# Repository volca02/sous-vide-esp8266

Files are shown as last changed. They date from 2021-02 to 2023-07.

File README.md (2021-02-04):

# sous-vide-esp8266

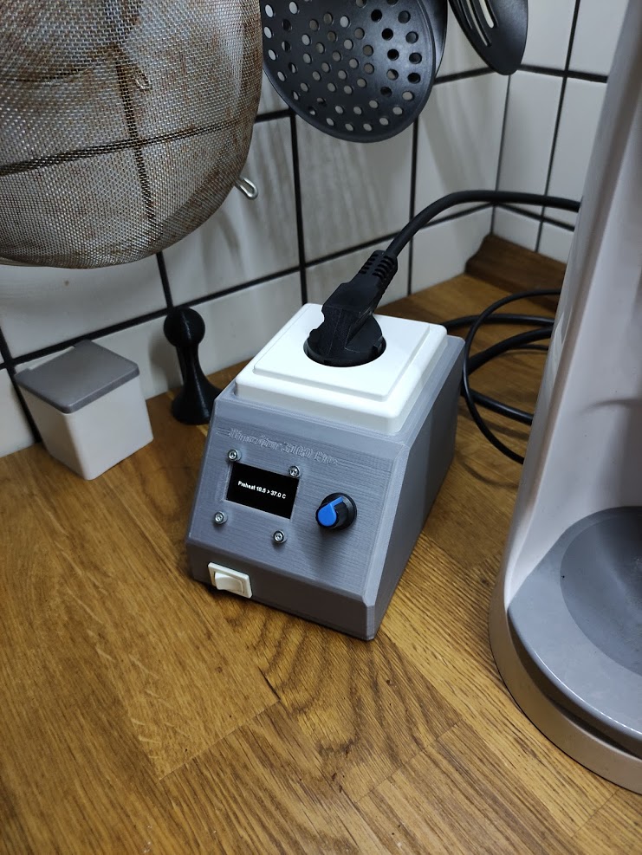
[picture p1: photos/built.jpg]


This project implements a simple timer and PID controller for a dumb slow cooker to become both a timer enabled slow cooker and a simple sous-vide cooker.

## About

The goal is to have a solid state relay control a simple crock-pot (or other compatible simple slow cooker that comes without any electronics). The usage of such contraption is both to add a timer to that slow cooker, and optionally hold a set temperature (when PID control is enabled in setup screen).

## Materials

You will need a couple of components:
 * [Wemos D1 Mini - or a clone](https://www.aliexpress.com/item/32681374223.html?spm=a2g0s.9042311.0.0.36504c4dLBnw4e)
 * [DS18B20 Waterproof Temp sensor](https://www.aliexpress.com/item/32305869288.html?spm=a2g0s.9042311.0.0.36504c4dLBnw4e)
 * [Solid state relay (DC control, AC output)](https://www.aliexpress.com/item/4000045425145.html?spm=a2g0s.9042311.0.0.36504c4dLBnw4e)
 * [SH1106Spi display](https://www.aliexpress.com/item/32844104782.html?spm=a2g0s.9042311.0.0.27424c4d58Iwcy)
 * [Rotary encoder](https://www.aliexpress.com/item/32915420023.html?spm=a2g0s.9042311.0.0.27424c4d58Iwcy)
 * Power cable
 * 5V power adaptor circuit (i.e. something that converts wall socket power to 5V for the Wemos D1)
 * Your local wall mounted power socket (or a cable power socket)
 * An enclosure - a 3d printable model is in [model/](model/) directory (written in openSCAD) - I used universal pcb mounted into the frame, and an a gutted old phone charger for the power supply (so the power supply mount will have to be modified for your situation). Lacking any other, I used M3/16 screws everywhere but the display, which uses 4x M3/10 screws (16 were too long). Sorry the code is a bit messy.

## Wiring

- `GND` is the D1's ground pin
- `3.3V` is the D1's 3V pin

### Temperature sensor

The Black wire connects to `GND`, Red wire to `3.3V`, Yellow wire to `D4`

### Solid state relay

The DC part connects `-` to `GND`,  `+` to `D8`
The AC part connects one power wire through the relay (as appropriate to your country). Ground wire connects directly through to the output socket.

### Display

These are the display's connections:

 * `D7` - `SDA`
 * `D5` - `SCK`
 * `D3` - `RST`
 * `D1` - `DC`
 * `GND` - `CS`
 * `3.3V` - `VDD`

### Rotary encoder

Due to the limited number of pins, A0 is used as a button detection pin.

 * `3.3V` - pin marked `5V`
 * `GND` - `GND`
 * `A0` - `KEY`
 * `D2` - `S1`
 * `D0` - `S2`

 ### Power adaptor

 The input power gets connected to the power adaptor.
 Power adaptor output connects to `5V` and `GND` leads of the Wemos D1.

### Assembly photos

 Here are some assembly photos for easier orientation:
 
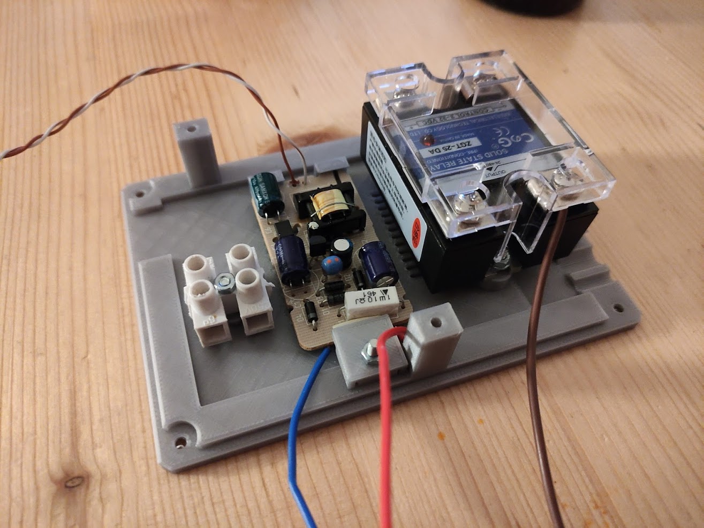
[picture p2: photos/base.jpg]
 
 
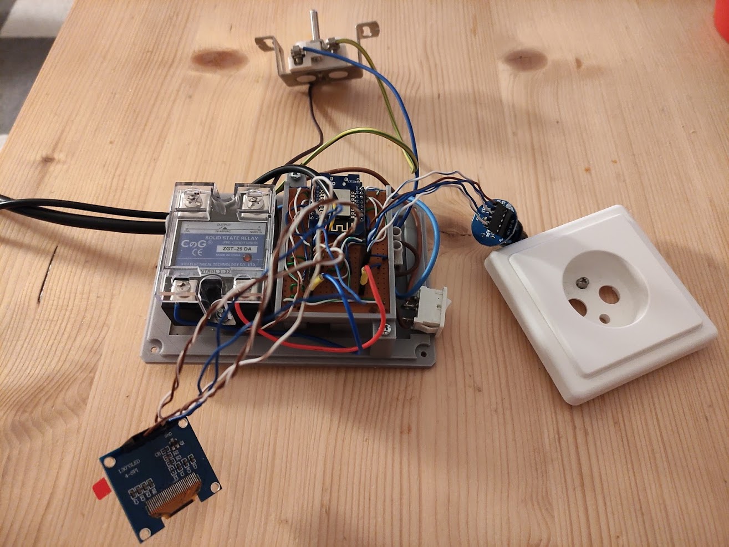
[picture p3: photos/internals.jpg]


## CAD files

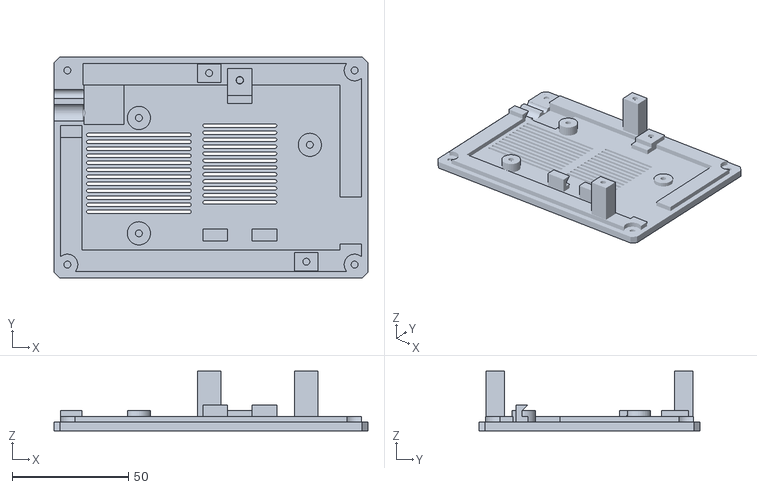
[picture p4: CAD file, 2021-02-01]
model/bottom.stl
135.0 x 95.0 x 25.8

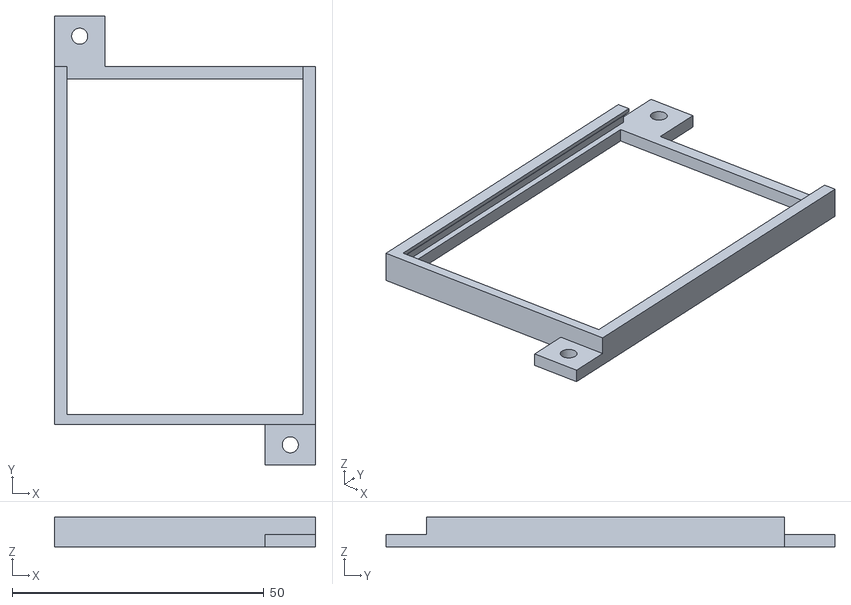
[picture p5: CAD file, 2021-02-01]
model/frame.stl
51.8 x 89.1 x 5.90

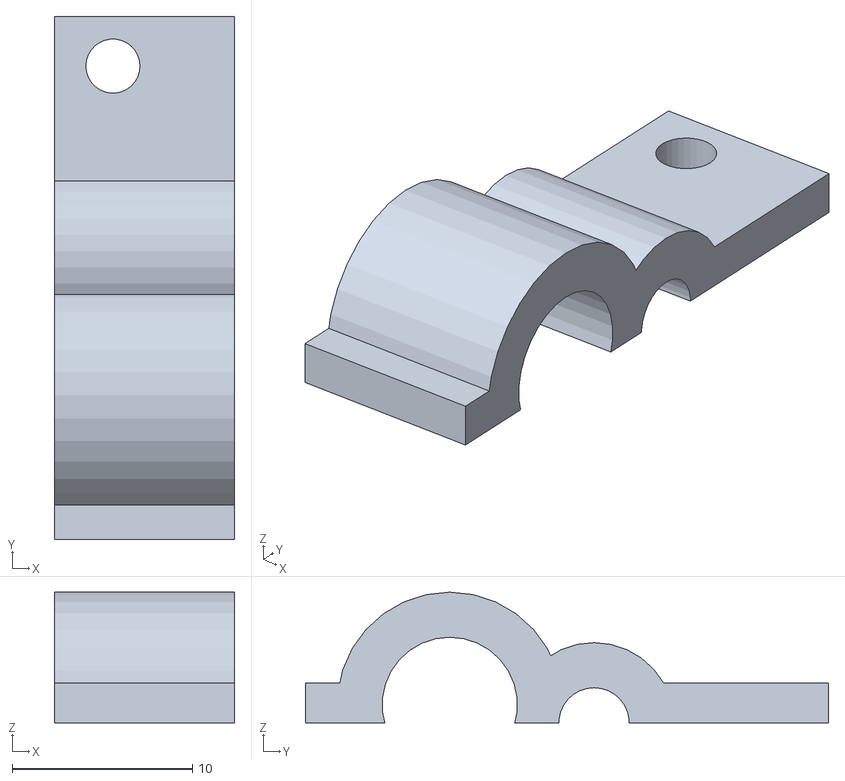
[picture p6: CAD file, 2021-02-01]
model/power_clamp.stl
10.0 x 29.0 x 7.25

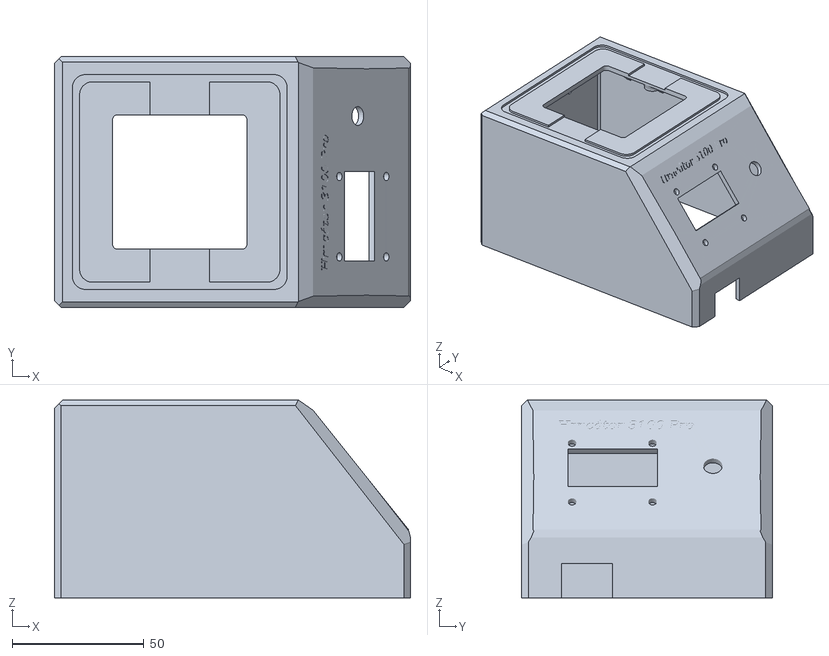
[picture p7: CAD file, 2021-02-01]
model/top.stl
135.0 x 95.0 x 75.0

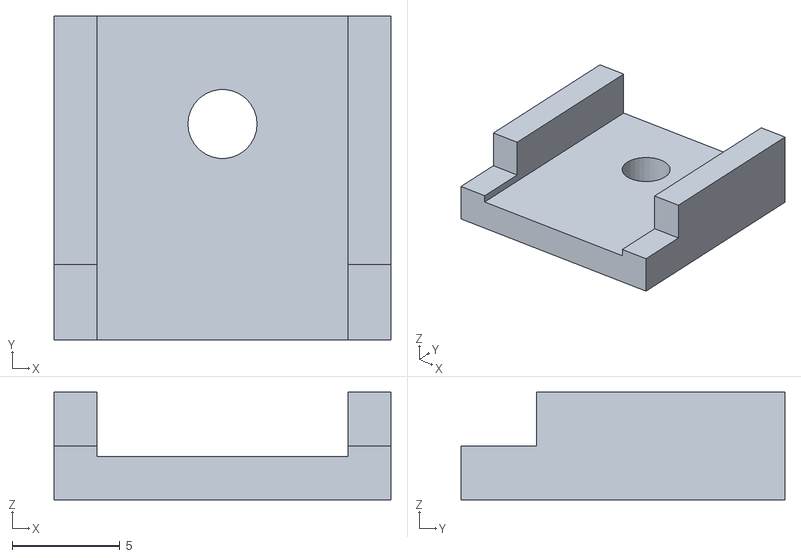
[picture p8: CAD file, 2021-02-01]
model/ps_clamp.stl
15.6 x 15.0 x 5.00

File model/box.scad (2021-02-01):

$fn = 30;

// Dimensions of the base box shape
width = 95;
top_depth = 95;
depth = top_depth + 40;
height = 75;
front_height = height - 50;

fp_angle = 51.3; // todo: use atan or trigonometry to make this in sync

wall = 2.5;
delta = 0.01;

psocket_hole_span = 60;
psocket_hole_d    = 3;
psocket_key_w     = 2.3;
psocket_key_span  = 70;
psocket_hole_h    = 3;

// front panel
encoder_d = 7.2;

// display part dimensions
display_w = 34.0;
display_h = 18.2;

screw_hole_d = 3.2;

// display holes
disp_hole_d = screw_hole_d;

disp_hole_top = 3.0; // above display edge
disp_hole_bottom = 28.5; // relative to the top hole
disp_hole_span   = 30.5; // left to right, centered with display

// switch dimensions
switch_w = 19.5;
switch_ww = 20.1;
switch_h = 13;
switch_lip = 1.2;
switch_x = 15;
switch_depth = 22;

// power supply
ps_w = 31.8;
ps_d = 59;
ps_x = 64;
ps_y = 30;
ps_h = 2.5; // we have to rise the pcb of the ps this much in order to fit the bottom mounted parts

// solid state relay
ssr_w = 45;
ssr_d = 58;
ssr_h = 33;
ssr_x = 14;
ssr_y = 26;

// screw-in mounts
choc_w = 22;
choc_d = 20.5;
choc_h = 18;
choc_x = 99;
choc_y = 20;

// power in lead-in
powin_off = 15.5;
powin_w = 10;
powin_d = 29.5;
powin_cable_d = 7.5;
temp_cable_d = 3.9;
powin_c1_y = 8;
powin_c2_y = 16;
powin_c1_z = 1;
powin_c2_z = 0;

// pcb mount pillars
pcb_x = 101;
pcb_y = -44.5;
pcb_d = 8;
pcb_w = 10;
pcb_h = 22;

// real pcb dimensions
pcb_r_w = 49.3; // slightly more than pcb (48.8) so we can slide it in
pcb_r_l = 66.6;
pcb_r_h = 1.4;

/*

  TODO:
  * test fit:
    X display
    X encoder
    - cable leadin
    - probe leadout
    X switch cutout
    X screw fit

  * mount points
    X ssr
    - power supply
    X main board
    X chocolate

  * models
    - Beautiful knob
  */

module rounded_cube(dim = [], d = 4) {
    // TODO: Use union (4 cylinders, 2 cubes) instead. this is expensive without a good reason
    hull() {
        translate([d/2,d/2,0]) cylinder(d=d, h=dim[2]);
        translate([dim[0]-d/2,d/2,0]) cylinder(d=d, h=dim[2]);
        translate([d/2,dim[1]-d/2,0]) cylinder(d=d, h=dim[2]);
        translate([dim[0]-d/2,dim[1]-d/2,0]) cylinder(d=d, h=dim[2]);
    }
}

module power_socket() {
    translate([-40,-40,0]) difference() {
        union() {
            difference() {
                rounded_cube([80,80,9.8],d=10);
                translate([1.5,1.5,-1.5]) rounded_cube([77,77,9.8]);
            }
            translate([15/2,15/2,9.8]) rounded_cube([65,65,3.5]);
            translate([40,40,-3]) cylinder(d=42.3,h=16);
            translate([20,15,-25]) rounded_cube([40,50,25]);
        }

        translate([40,40,9.8+3.5-16+delta]) cylinder(d=38.5,h=16);
    }
}

// power socket frame - subtracted from the top panel to allow the socket
// to be slightly (1mm) inserted into the panel
module socket_frame(h=2) {
    wid = 81.5;
    iwid = 76;
    dif = wid-iwid;
    translate([-wid/2,-wid/2,0]) difference() {
        rounded_cube([wid,wid,h],d=10);
        translate([dif/2,dif/2,-0.1]) rounded_cube([iwid,iwid,h+0.2],d=9.8);
    }
}

module bracket(h=0.5) {
    br_w = 14.1;
    br_h = 22.5;

    difference() {
        union() {
            translate([br_w/2,0,h/2]) cube([br_w,br_h,h],center=true);
            translate([6.05,0,-wall-0.2]) cylinder(d=psocket_hole_d,h=wall,$fn=30);
        }
      //  translate([11.0+3.3/2,0,-delta+h/2]) cube([3.3,psocket_key_w,h+0.2],center=true);
    }
}

module mounting_brackets(h=0.5) {
    sp   = 47.9;

    // spaced
    for (a=[0,180]) rotate([0,0,a]) translate([sp/2,0,0]) bracket(h);
}

module socket_pillar() {
    extd = psocket_hole_d+2*wall;
    difference() {
        union() {
            cylinder(d=extd,h=psocket_hole_h);
            translate([0,0,psocket_hole_h-2]) cylinder(d2=extd+1,d1=extd,h=2);
        }
        translate([0,0,-0.1]) cylinder(d=psocket_hole_d,h=psocket_hole_h+0.2);
    }
}

module mounting_pillars(h=0.5) {
    sp   = psocket_hole_span;

    // spaced
    for (a=[0,180]) rotate([0,0,a]) translate([sp/2,0,0]) socket_pillar();
}

// positive geometry wall power socket mount, placed directly on the top surface
module psocket_mount() {
    rotate([0,0,90]) translate([0, -width/2, -wall]) union() {
        difference() {
            union() {
                cube([top_depth, width, wall]);
                // strengthening for the nuts/bolts
                translate([top_depth/2,width/2,-psocket_hole_h]) mounting_pillars();
            }
            translate([top_depth/2,width/2,0]) {
                translate([0,0,wall-1]) socket_frame();
                translate([-51/2,-51/2,-delta]) rounded_cube([51,51,10]);
                translate([0,0,wall-1]) mounting_brackets(h=1+delta);

            }
        }
    }
}

module side_shape() {
    polygon([
                    [0,0],
                    [0,height],
                    [top_depth, height],
                    [depth, front_height],
                    [depth, 0]
            ]);
}

module base_shape() {
    translate([0,width/2,0]) rotate([90,0,0]) linear_extrude(height=width) side_shape();
}


module inner_cavity() {
    translate([0,width/2,0]) difference() {
        w2 = 2*wall;
        union() {
            translate([0,-wall,0]) rotate([90,0,0]) linear_extrude(height=width-w2) offset(r=-wall) side_shape();
            translate([wall,-width+wall,-delta]) cube([depth-w2,width-w2,3*wall]);
        }

        for (x=[20,40,60,80]) {
            translate([x,0,height-20]) rotate([45,0,0]) cube([wall, 40, 40]);
            translate([x,-width-wall,height-20]) rotate([45,0,0]) cube([wall, 40, 40]);
        }
    }
}


//inner_cavity();

//translate([top_depth/2,0,height-1]) power_socket();


module display_cutter() {
    cube([display_w,display_h,2*wall]);
    for(y=[display_h+disp_hole_top,display_h-disp_hole_bottom+disp_hole_top]) {
        for(x=[0,disp_hole_span]) {
            translate([x+disp_hole_d/2,y,0]) cylinder(d=disp_hole_d,h=2*wall);
        }
    }
}


module encoder_cutter() {
    cylinder(d=encoder_d,h=2*wall);
}

module front_panel() {
/*    difference() {*/
//      cube([70,50,wall]);
    union() {
        translate([5,20,-delta]) display_cutter();
        translate([60,30,-delta]) encoder_cutter();
        translate([ 1, 48, wall - 0.15 ]) linear_extrude(height    = 1,
                                                         convexity = 4)
                text("Hrncátor 3100 Pro", font = "DejaVu Serif:style=Italic", size = 4);

        translate([5,17,wall-delta]) cube([display_w,1,1]);
  }
}

module raw_body() {
    align=3.2; // an ugly method for sure, but lets us do the positioning of front panel stuff easier
    union() {
        difference() {
            base_shape();
            inner_cavity();
            translate([0,-width/2,height-wall-delta]) cube([top_depth, width, wall+delta*2]);
//            translate([depth-align,-width/2+25/2,front_height]) rotate([0,0,90]) rotate([fp_angle,0,0]) translate([0,0,-delta]) cube([70,50,2*wall]);
            translate([depth-align,-width/2+25/2,front_height]) rotate([0,0,90]) rotate([fp_angle,0,0]) front_panel();
        }

        translate([top_depth/2,-width/2,height]) psocket_mount();
    }
}

// half of the cutters, mirrored later for accuracy
module cutter_half(offseting=0) {
    off = 5;
    translate([-1+depth/2,width/2+off/2,height + off/2]) rotate([45,0,0]) cube([depth,10-offseting,10-offseting],center=true);
    translate([off/2+top_depth,width/2+off/2,height - off/2]) rotate([0,52,0]) rotate([45,0,0]) cube([depth,10-offseting,10-offseting],center=true);


    translate([top_depth+2,width/2+off/2,height+3]) rotate([0,0,-90]) rotate([55,0,0]) cube([depth,10-offseting,10-offseting],center=true);


    translate([-1,width/2+off/2,height+3]) rotate([0,0,-90]) rotate([45,0,0]) cube([depth,10-offseting,10-offseting],center=true);

    translate([depth+5.3,width/2+off/2,front_height - off/2]) rotate([0,0,-90]) rotate([15,0,0]) cube([depth,10-offseting,10-offseting],center=true);

    // corners
    translate([0,width/2,0]) rotate([0,0,45]) translate([0,0,(height+1)/2]) cube([3.5-offseting,3.5-offseting,height+2],center=true);
    translate([depth,width/2,0]) rotate([0,0,45]) translate([0,0,(height+1)/2]) cube([3.5-offseting,3.5-offseting,height+2],center=true);
}

module cutters(off = 0) {
    cutter_half(off);
    mirror([0,1,0]) cutter_half(off);
}

module pillar(d,w,h,s=-1) {
    dw = d+2*w;
    union() {
        difference() {
            cylinder(d=dw,h=h);
            translate([0,0,-delta]) cylinder(d=d,h=h-dw+2*delta);
            if (s != 0) {
                translate([0,0,h]) rotate([0,-s*45,0]) cube([4*dw,dw,dw], center=true);
            }
        }
    }
}

module pillars(d=3,w=wall,h=22,en=1) {
    // all corners have screw pillars
    pd = 9 + wall;
    for (y = [-width/2+pd/2,width/2-pd/2]) {
        for (x = [pd/2,depth-pd/2]) {
            xs = x - depth/2;
            translate([x,y,0]) pillar(d=d,w=w,h=h,s=en*abs(xs)/xs);
        }
    }
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

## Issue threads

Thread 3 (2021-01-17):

Add temperature history

volca02, 2021-01-17:
Add a simple (1 pt per minute) temperature logger. Memory should be able to hold 1440 float values, if not, convert to fixed point int16_t. Add json url to dump the values for a web based graph or similar.

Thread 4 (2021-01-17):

Add PID tuning code

volca02, 2021-01-17:
A special mode (maybe when encoder is held on bootup) that would do automatic pid tuning and write the result to SPIFFS. Then a code that reads this on bootup and gives these to AutoPID class instance.

This bootup special menu could also be used to set wifi and other things...

volca02, 2021-02-05:
implemented in 4d5d5553b20a85f5fcbc73b2e2dd840e69db3d70, does not work yet. Needs to be fixed

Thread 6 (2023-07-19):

Dependency and build errors

biuklija, 2023-07-19:
I am unable to build this project due to the following issues:

- Library dependency "562" is not automatically resolved and I can't pinpoint what this library dependency is supposed to be.

- The SH1106Spi library is not defined in the dependencies, although this is a minor issue.

- I'm getting multiple build errors. First one:
`src\main.cc:168:22: error: 'IOTWEBCONF_STATE_ONLINE' was not declared in this scope; did you mean 'IOTWEBCONF_DEBUG_LINE'?
Compiling .pio\build\d1_mini\lib6ae\ESP8266WiFi\ESP8266WiFiGratuitous.cpp.o
src\main.cc:169:25: error: 'IOTWEBCONF_STATE_NOT_CONFIGURED' was not declared in this scope; did you mean 'IOTWEBCONF_HTML_CONFIG_VER'?
*** [.pio\build\d1_mini\src\main.cc.o] Error 1`

- Second build error:
`lib\encoder\ClickEncoder.cpp: In member function 'void ClickEncoder::service()':
lib\encoder\ClickEncoder.cpp:223:69: error: no matching function for call to 'min(long unsigned int&, uint16_t&)'
223 |       doubleClickTicks -= min(millisSinceLastCheck, doubleClickTicks);`

Any assistance appreciated.

volca02, 2023-07-28:
Hey,

I've not used this device since the display broken ages ago, but tried fixing the build problems.

On my machine it now builds - I will be not able to test if it runs as well.

Here are the dependencies
```
Dependency Graph
|-- OneWire @ 2.3.7
|-- DallasTemperature @ 3.11.0
|-- AutoPID @ 1.0.4
|-- IotWebConf @ 3.2.1
|-- PubSubClient @ 2.8.0
|-- ESP8266 and ESP32 OLED driver for SSD1306 displays @ 4.4.0
|-- ClickEncoder @ 0.0.0-alpha+sha.9337a0c46c
|-- ArduinoOTA @ 1.0
```

biuklija, 2023-08-02:
Thank you, I'm waiting on some of the hardware so I'll test it out and report back.

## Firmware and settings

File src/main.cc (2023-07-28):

/* --------------------------------------------------------
   Sousvide/timer controller project.
   --------------------------------------------------------
*/

#include <Arduino.h>
#include <SH1106Spi.h>
#include <OneWire.h>
#include <DallasTemperature.h>
#include <AutoPID.h>
#include <ClickEncoder.h>

#include <ArduinoOTA.h>
#include <IotWebConf.h>
#include <IotWebConfUsing.h>
#include <PubSubClient.h>

#ifdef AUTOTUNER
#include <pidautotuner.h>
#endif

static int8_t ICACHE_FLASH_ATTR todigit(char ch) {
    if (ch >= '0' && ch <= '9')
        return ch - '0';

    return -1;
}

static bool validate_dec(const char *buf) {
    for (;*buf;++buf) {
        if (todigit(*buf) < 0)
            return false;
    }
    return true;
}

// ------------ IOT Web Conf Code ------------
#define NUM_LEN 16 // for the regulator constants

const float pid_loop_interval = 5000; // in ms, loop interval of the pid

bool config_mode = false; // enabled by pressing encoder while starting the device

// this is IOTWebconf side config, with conversion methods to get the values
class Config {
public:
    // PID constants
    char kp[NUM_LEN] = "0.12";
    char ki[NUM_LEN] = "0.0003";
    char kd[NUM_LEN] = "0";

    float get_kp() const { return atof(kp); }
    float get_ki() const { return atof(ki); }
    float get_kd() const { return atof(kd); }

    // temperature offset
    char temp_offset[NUM_LEN] = "0";

    float get_temp_offset() const { return atof(temp_offset); }

    void move_temp_offset(int steps, float step = 0.1) {
        float cur = get_temp_offset();
        cur += step * steps;
        snprintf(temp_offset, NUM_LEN, "%f", cur);
    }

    // MQTT Server
    char mqtt_client_id[20];
    char mqtt_server[41] = "";
    char mqtt_port[NUM_LEN] = "1883";
    char mqtt_user[21] = "";
    char mqtt_pass[21] = "";
    char mqtt_topic_prefix[41] = "sousvide";
};

class NetworkHandler {
public:
// -- Initial name of the Thing. Used e.g. as SSID of the own Access Point.
    const char *thing_name = "SousVide";
    const char *wifi_initial_pwd = "password123456"; // password for initial ap
    const char *config_version = "cv1";

    NetworkHandler(Config &config)
            : config(config)
            , dnsServer()
            , server(80)
            , iotWebConf(thing_name,
                         &dnsServer,
                         &server,
                         wifi_initial_pwd,
                         config_version)

            , controller_group("Controller", "")
            , kp("Kp",
                 "kp",
                 config.kp,
                 NUM_LEN,
                 nullptr,
                 "Kp regulator constant",
                 "step='0.0001'")
            , ki("Ki",
                 "ki",
                 config.ki,
                 NUM_LEN,
                 nullptr,
                 "Ki regulator constant",
                 "step='0.0001'")
            , kd("Kd",
                 "kd",
                 config.kd,
                 NUM_LEN,
                 nullptr,
                 "Kd regulator constant",
                 "step='0.0001'")
            , temp_offset("Temp offset",
                          "temp_offset",
                          config.temp_offset,
                          NUM_LEN,
                          nullptr,
                          "Greater val. means the sensor indicates less than real temp.")
            , mqtt_group("MQTT Connection", "")
            , mqtt_server("MQTT Server", "mqtt_server", config.mqtt_server, 40)
            , mqtt_port("MQTT Port",
                        "mqtt_port",
                        config.mqtt_port,
                        NUM_LEN,
                        nullptr,
                        "MQTT Server Port")
            , mqtt_user("MQTT User", "mqtt_user", config.mqtt_user, 20)
            , mqtt_pass("MQTT Password", "mqtt_pass", config.mqtt_pass, 20)
            , mqtt_topic(
                      "MQTT Topic", "mqtt_topic", config.mqtt_topic_prefix, 40)
    {}

    void setup() {
        controller_group.addItem(&kp);
        controller_group.addItem(&ki);
        controller_group.addItem(&kd);
        controller_group.addItem(&temp_offset);

        mqtt_group.addItem(&mqtt_server);
        mqtt_group.addItem(&mqtt_port);
        mqtt_group.addItem(&mqtt_user);
        mqtt_group.addItem(&mqtt_pass);
        mqtt_group.addItem(&mqtt_topic);

        iotWebConf.addParameterGroup(&controller_group);
        iotWebConf.addParameterGroup(&mqtt_group);

        // TODO: skipAPStartup/forceAPMode
        iotWebConf.init();

        server.on("/", [&] { handle_root(); });
        server.on("/config", [&] { iotWebConf.handleConfig(); });
        server.onNotFound([&] { iotWebConf.handleNotFound(); });
        iotWebConf.setFormValidator([&] (iotwebconf::WebRequestWrapper*) { return validate_config(); });

        server.begin();
    }

    void handle_root() {
        // -- Let IotWebConf test and handle captive portal requests.
        if (iotWebConf.handleCaptivePortal()) {
            // -- Captive portal request were already served.
            return;
        }

        // AP mode config portal
        auto state = iotWebConf.getState();
        if (state == iotwebconf::ApMode
            || state == iotwebconf::NotConfigured)
        {
            iotWebConf.handleConfig();
            return;
        }

        String s =
            "<!DOCTYPE html><html lang=\"en\"><head><meta "
            "name=\"viewport\" content=\"width=device-width, "
            "initial-scale=1, user-scalable=no\"/>"
            "<title>SousVide status</title></head><body> PLACEHOLDER!"
            "<a href='config'>configuration</a>"
            "</body></html>\n";

        server.send(200, "text/html", s);
    }

    void update() {
        iotWebConf.doLoop();
        server.handleClient();
    }

    void saveConfig() {
        iotWebConf.saveConfig();
    }

protected:
    bool validate_config() {
        bool valid = true;

        auto mqtt_p = server.arg(mqtt_port.getId());
        if (!validate_dec(mqtt_p.c_str())) {
            mqtt_port.errorMessage = "MQTT Port expects a number!";
            valid = false;
        }

        return valid;
    }

    Config &config;
    DNSServer dnsServer;
    WebServer server;
    IotWebConf iotWebConf;

    // setup params
    IotWebConfParameterGroup controller_group;
    IotWebConfNumberParameter kp;
    IotWebConfNumberParameter ki;
    IotWebConfNumberParameter kd;
    IotWebConfNumberParameter temp_offset;

    IotWebConfParameterGroup mqtt_group;

    IotWebConfTextParameter mqtt_server;
    IotWebConfNumberParameter mqtt_port;
    IotWebConfTextParameter mqtt_user;
    IotWebConfTextParameter mqtt_pass;
    IotWebConfTextParameter mqtt_topic;
};

// -------------------- HW Config --------------------
using Display = SH1106Spi;

#define OLED_RST_PIN D3
#define OLED_DC_PIN  D1

#define TEMP_SENSOR_PIN D4

#define ROT_KEY_PIN A0
#define ROT_S1_PIN  D0
#define ROT_S2_PIN  D2
#define ROT_STEPS_PER_NOTCH 4

#define RELAY_PIN   D8

const char *version_str = "0.0.2";

constexpr byte CURSOR_SIZE = 5;

/**
Pinout/connection diagram:

Display (3V3 and GND connected as indicated on display):
  D7 -> SDA
  D5 -> SCK
  D3 -> RST
  D1 -> DC
  GND -> CS

Temp sensor (3V3 and GND connected to red/black respectively):
  D4 -> Yellow wire (onewire data)

Rotary encoder:
  A0 -> Key
  D2 -> S1
  D0 -> S2

Solid state relay:
  D8  -> + port
  GND -> - port
*/

/**
TODO:
 * NTP support, display current time in corner
 * fahrenheit as a second value when setting temp (no conversion needed when cooking by the book)
 * Controller constants can't be set over MQTT. Diagnose that

DONE:
 X SousVide mode does NOT end after timer ends
 X Re-setting to setup does not put the remaining time back
 X Moving the remaining time should round it down/up as appropriate to the nearest multiple of the 15min interval
 X Ready after initial heatup - require one press of the encoder after preheat before activating timer
   - also after return to setup?
 X Setup phase screen saving (inactive for too long - blank the screen)
 X Config mode
 X MQTT support
   - report temperature, estimated time(stamp) of end of cooking
   - set mode, disable cooking remotely, set different temperature, timer
 X Configuration persistence (via IOTWebConf)
 X Temperature offset option - measure 37C with a medical thermometer, remember the diff
 X FIX PID autotune. Currently does not work
*/


/** This forces ClickEncoder to use A0 as button input
 * (on wemos d1 we don't have a different pin to use!)
 * @note overriden by hand, the original class does not do this right
 */
class AnalogClickEncoder : public ClickEncoder
{
  public:
    explicit AnalogClickEncoder(
            int8_t A, int8_t B, int8_t BTN = -1,
            uint8_t stepsPerNotch = 4, bool active = LOW,
            int16_t rangeLow = 0, int16_t rangeHigh = 512)
        : ClickEncoder(A, B, BTN, stepsPerNotch, active)
    {
        pinMode(pinBTN, INPUT);

        anlogActiveRangeLow = rangeLow;
        anlogActiveRangeHigh = rangeHigh;
        analogInput = true;

        if (anlogActiveRangeLow > anlogActiveRangeHigh) {    // swap values if provided in the wrong order
            int16_t t = anlogActiveRangeLow;
            anlogActiveRangeLow = anlogActiveRangeHigh;
            anlogActiveRangeHigh = t;
        }
    }
};


void draw_cursor_horizonal(Display &display, byte x, byte y, bool cross = false) {
    display.drawLine(x, y,
                     x + CURSOR_SIZE, y + CURSOR_SIZE/2);

    display.drawLine(x, y + CURSOR_SIZE,
                     x + CURSOR_SIZE, y + CURSOR_SIZE/2);

    display.drawLine(x, y,
                     x, y + CURSOR_SIZE);

    if (cross) {
        display.drawLine(x, y + CURSOR_SIZE /2,
                         x + CURSOR_SIZE, y + CURSOR_SIZE / 2);
    }
}

// Handles the cooking time
class Timer {
public:
    Timer(Timer &) = delete;
    Timer() = default;

    static const constexpr unsigned long MAX_TIMER = 24 * 60 * 60 * 1000; // 1 day

    void run() { set_enabled(true); };
    void stop() { set_enabled(false); };

    void reset() { ran = false; }

    void pause() {
        ran = false;
        enabled = false;
        if (target > elapsed) {
            target = target - elapsed;
        } else {
            target = 0;
        }
        elapsed = 0;
    }

    void set_enabled(bool en) {
        if (enabled == en) return;

        enabled = en;

        if (en) {
            prev = millis();
            ran = true;
        }
    }

    void set_target(unsigned long tgt) { target = tgt; }
    unsigned long get_target() const { return target; }

    unsigned long get_remaining() const {
        if (elapsed >= target) return 0;
        return target - elapsed;
    }

    void move_target(int amount, unsigned long interval = 15 * 60 * 1000) {
        // the two weird math ops below guarantee us that we will round up to
        // nearest multiple of interval but move the value at the same time
        if (amount < 0) {
            if (target > interval)
                target = interval * ((target - 1) / interval);
            else
                target = 0;
        } else {
            target = interval * ((target + interval) / interval);
            if (target > MAX_TIMER) target = MAX_TIMER;
        }
    }

    bool is_enabled() const { return enabled; }
    bool done() const { return elapsed >= target && ran; }

    void update() {
        if (enabled && prev) {
            unsigned long now = millis();
            elapsed += now - prev;
            prev = now;
        }
    }

protected:
    bool ran = false; // set after first timer start. Distinguishes done with setup in ui
    bool enabled = false;
    unsigned long prev    = 0;
    unsigned long elapsed = 0;
    unsigned long target  = 0;
};

class TempSensor {
public:
    TempSensor(TempSensor &) = delete;

    TempSensor(uint8_t pin) :
        oneWire(pin),
        dallas(&oneWire),
        offset(0)
    {}

    void begin(float off) {
        offset = off;
        dallas.begin();

        //
        dallas.getAddress(tempDeviceAddress, 0);
        dallas.setResolution(tempDeviceAddress, resolution);
        dallas.setWaitForConversion(false);
        dallas.requestTemperatures();
        // calculate the delay needed to read the temp
        delayInMillis = 750 / (1 << (12 - resolution));
        last_update = millis();
    }

    float get() {
        unsigned long time = millis();

        // either time passed or overflowed
        if (time - last_update > delayInMillis) {
            dallas.requestTemperatures();
            temp = dallas.getTempCByIndex(0);
            last_update = time;
            dallas.requestTemperatures();
            // TOO: Could record temp history here...
        }

        // in case someone measured and set this, we add offset here
        return temp + offset;
    }

    unsigned long last_update = 0;
    float temp = 0;
    OneWire oneWire;
    DallasTemperature dallas;
    float offset;

    int resolution = 10;
    DeviceAddress tempDeviceAddress;
    unsigned long delayInMillis = 0; //
};

/** PID seems not like a good fit for us (oveshoot, nonlinear)
 * this implements a bang-bang controller with a nonsymmetrical hysteresis
 * instead.
 * What it does is try to oscillate betwen setpoint - undershoot and setpoint
 * but it also checks for overshoot by not stepping over the setpoint - overshoot threshold
 * while heating up without "PWM"
 */
class BangController {
public:
    BangController(double *input,
                   double *setpoint,
                   double *output,
                   double overshoot = 1.5,
                   double undershoot = 0.5)
        : _input(input)
        , _setpoint(setpoint)
        , _output(output)
        , _overshoot(overshoot)
        , _undershoot(undershoot)
        , _last_switch(0)
    {}

    void run() {
        auto min = get_falling_min();
        auto max = get_growing_max();
        auto now = millis();

        if (_heating && (*_input > max) && ((now - _last_switch) > _period)) {
            set_heating(false);
            _last_switch = now;
        } else if (!_heating && (*_input < min)
                   && ((now - _last_switch) > _period))
        {
            set_heating(true);
            _last_switch = now;
        }
    }

    void reset() {
        set_heating(false);
    }

    void set_overshoot(float over)    { _overshoot  = over; }
    void set_undershoot(float under)  { _undershoot = under; }
    void set_period(unsigned long p)  { _period     = p; }

private:
    void heating_on() {
        set_heating(true);
    };

    void heating_off() {
        set_heating(false);
    };

    void set_heating(bool ena) {
        if (_heating == ena) return;

        _heating = ena;
        *_output = _heating ? 1.0f : 0.0f;
    }

    double get_growing_max() { return *_setpoint - _overshoot; }
    double get_falling_min() { return *_setpoint - _undershoot; }

    double *_input, *_setpoint, *_output;

    bool _heating = true;

    float _overshoot = 1.5;
    float _undershoot = 0.5;

    unsigned long _last_switch = 0;
    unsigned long _period = 5000; // 5s default period
};

/*
  Phases:
   1. Configuration after powerup
   2. Heating
   3. Prepared - cooking
   4. Done. Blink finished

 */
class Controller {
public:
    static const constexpr float MIN_TEMP = 0.0;
    static const constexpr float MAX_TEMP = 100.0;
    static const constexpr float DEFAULT_TEMP = 50.0;

    Controller(Controller &) = delete;

    Controller(Config &conf, uint8_t pin, TempSensor &temp, Timer &timer)
            : conf(conf)
            , relay_pin(pin)
            , temp_sensor(temp)
            , timer(timer)
            , pid(&pid_input, &pid_setpoint, &pid_relayState,
                  pid_loop_interval, conf.get_kp(), conf.get_ki(), conf.get_kd())
    {
    }

    static const constexpr double preheat_threshold = 1.0; // +- this means we're in range

    void begin() {
        // enable pinout of the relay, and switch heating off as default...
        pinMode(relay_pin, OUTPUT);
        heating_off();

        // bangbang is used outside of the 4 degress range of the target
        pid.setBangBang(4);
        pid.setTimeStep(pid_loop_interval);
        set_gains();
    }

    void set_gains() {
        // we set gains here again because network.setup() read the config for us
        pid.setGains(conf.get_kp(), conf.get_ki(), conf.get_kd());
    }

    double get_control_value() { return pid.getPulseValue(); }

    // **** this section enables/disables the controller ****
    void set_enabled(bool ena) {
        if (ena == enabled) return;

        enabled = ena;

        if (ena) {
            pid.run();
        } else {
            // also handle timer
            timer.pause();
            pid.stop();
            heating_off();
            started = false;
            preheating = true;
            did_reset = false;
        }
    }

    void enable() {
        set_enabled(true);
    }

    void disable() {
        set_enabled(false);
    }

    bool is_enabled() const { return enabled; }
    bool is_heating() const { return heating; }
    bool is_pid_enabled() const { return pid_mode; }
    double get_target_temp() const { return pid_setpoint; }

    bool is_started() const { return started; }
    void start() { started = true; }

    // **** This section is dedicated to settings ***
    void set_use_pid(bool use_pid) {
        pid_mode = use_pid;
    }

    /// sets target temperature and enables pid mode, or disables pid for negative temps
    void set_target_temp(float temp) {
        pid_mode = true;
        pid_setpoint = temp;

        if (temp <= MIN_TEMP) {
            temp = MIN_TEMP;
            pid_mode = false;
        } else if (temp >= MAX_TEMP) {
            temp = MAX_TEMP;
        }
    }

    void move_target_temp(int steps, float step = 1.0) {
        // each step is 0.1 of a degree. we use acceleration to move faster
        set_target_temp(pid_setpoint + steps * step);
    }

    /** returns true if the controller is in pre-heat mode.
     * this only applies to PID mode, normal mode does not have any pre-heat phase
     */
    bool is_preheating() {
        return pid_mode && preheating;
    }

    void update() {
        // if timer says so, we stop doing what we're doing
        if (timer.done()) {
            disable();
            return;
        }

        // early exit if disabled. This means PIDTuner can override and use
        // set_heater without us immediately switching it off due to disabled
        // controller
        if (!enabled) return;

        // below, all code is with enabled on...
        if (!pid_mode) {
            started = true; // no need to wait here, just override it...
            set_heating(true);
            timer.set_enabled(true);
            timer.update();
            return;
        }

        // refresh the temperature
        pid_input = temp_sensor.get();

        // pid mode follows:
        pid.run();

        set_heating(pid_relayState);

        bool atPoint = pid.atSetPoint(preheat_threshold);

        // first time we get close to the set point, we reset the pid control values)
        // this stops some of the overshoot due to the integral growing out of range
        if (atPoint && !did_reset) {
            // this is a naiive implementation of Anti-Integral Windup
            did_reset = true;
            pid.reset();
        }

        // are we preheating or are we set around the target range?
        // once we get in the temp range, we dont't ever get out
        // unless we reset the whole process.
        // This mitigates the issue where we insert the food and
        // temp drops down, forcing us to wait for preheat again...
        if (preheating) preheating = !atPoint;
        timer.set_enabled(atPoint && started);
        timer.update();
    }
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
void loop()
{
    if (config_mode) ArduinoOTA.handle();
    network.update();

    // handle encoder input...
    static uint32_t last_service = 0;
    uint32_t ms = micros();

    // every millisecond we handle the encoder
    if (ms - last_service > 1000) {
        last_service = ms;
        encoder.service();
    }

    ui.update();

    mqtt.loop();

    // every ~minute we report to mqtt handler
    // - so in case MQTT is enabled, we get updates there and control commands back
    static unsigned long last_mqtt = 0;

    // every half minute is enough?
    if (ms - last_mqtt > 30000000) {
        last_mqtt = ms;

        Serial.println("MQTT update");
        const char *status = "unknown";

        switch (ui.infer_state()) {
        case UI::ST_AUTOTUNE: status = "autotune"; break;
        case UI::ST_CONFIG:   status = "config";   break;
        case UI::ST_DONE:     status = "done";     break;
        case UI::ST_SETUP:    status = "setup";    break;
        case UI::ST_PREHEAT:  status = "preheat";  break;
        case UI::ST_COOKING:  status = "cooking";  break;
        }

        mqtt.update(temp.get(), status);
    }
}

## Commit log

2021-01-17 First working prototype added
2021-02-01 adding 3d printable model parts and scad source code
    [bottom.stl, box.scad, frame.stl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]
2021-02-01 this (combined with other changes in main file) seem to make the encoder slightly more bearable
2021-02-01 Initial phase of fixes. * timer would not stop if the cooking was interrupted * encoder fixes (still jumps like crazy though) * time setting improvements (f.ex. holding down the button makes the step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
    [main.cc]
2021-02-04 * Added config mode (hold encoder on powerup) - enables setting Temp offset and doing pid autotune. ! PID Autotune does not yet seem to work though - WIP * Added config persistence * Added wifi based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
2021-02-07 * Fix for OTA * Fix for webserver not displaying * all UI Screens now render custom status text * Temperature measurement is now asynchronous * Fix for PID autotuner not working (missing init) * adde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
    [main.cc]
2021-02-08 Always report temperature
2021-02-13 v0.0.2 - programming screens while OTA is being done. Reset pid while first stepping into the range... Seems to still overshoot by 2.5 degrees, will try BangBang with hysteresis now.
    [main.cc]
